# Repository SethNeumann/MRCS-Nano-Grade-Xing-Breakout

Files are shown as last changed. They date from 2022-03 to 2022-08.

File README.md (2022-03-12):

# REPO NAME: MRCS-Nano-Grade-Xing-Breakout

## License: Creative Commons Attribution-NonCommercial-ShareAlike

There are plenty of good Arduino Grade Xing sketches. This board supports one by Jon Schmidt which uses the Nano's 8
analog inputs to monitor up 4 sets of sensors. It drives 2 servos for the crossing gates, 2 phases of LEDs
for the flashing lights and an output to drive a crossing bell sound module, like the ones from our friends
at Iowa Scaled Engineering.

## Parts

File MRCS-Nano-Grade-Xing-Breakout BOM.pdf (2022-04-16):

Qty | Value | Device | Package | Parts | Description
2 | CONNECTOR-M08LOCK | 1X08_LOCK | SENSOR0-3, SENSOR4-7 | Header 8
2 | M03LOCKx2 | 22X03_LOCK | A6, A7, SERVO1, SERVO2 | Header 3
2 | RPTH-R0 | CUT-R | R8, R9 | cuttable Resistor pad
| 1 .1 @ 25V | CAPPTH2 | C-PTH-0.100 | C2
| 2 10K | TRIM_US-RS3 | RS3 | R1, R2 | POTENTIOMETER
1 470 uF @ 16V CAP-POLPTH-3.5MM | E3.5-10 | C1
| 1 4700 | G08R | SIL9 | RN1 | SIL RESISTOR
| 1 5V PWR | CONNECTOR-DC-POWER-RA | DCJ0202 | J1 | DC POWER JACK
| 1 5V PWR | CONNECTOR-M04SCREW_LOCK | SCREWTERMINAL-3.5MM-4_LOCK | CON1 | Header 4
| 1 NANO | NANO | NANO | U$1 | Arduino Nano
| 1 Outputs | CONNECTOR-M08LOCK | 1X08_LOCK | J4 | Header 8
| 0 Unused I/O | CONNECTOR-M08LOCK | 1X08_LOCK | J2 | Header 8
| 2 15 pin | 0.100 x 15 female header | | N1, N2 | Nano Header
| 1 PCB | Grade Xing Controller | 69x99 | | PCB

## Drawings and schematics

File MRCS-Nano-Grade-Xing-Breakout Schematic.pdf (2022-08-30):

A

A

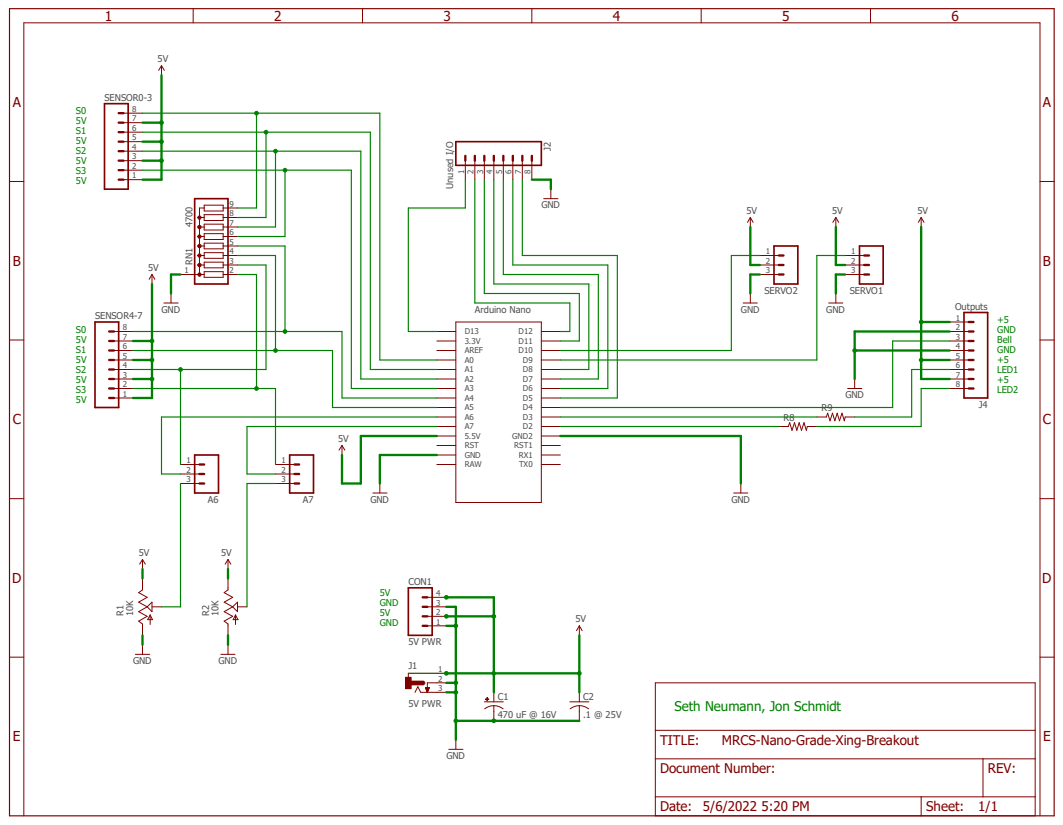
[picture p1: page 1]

Seth Neumann, Jon Schmidt

MRCS-Nano-Grade-Xing-Breakout

Document Number: | REV:

Date: 5/6/2022 5:20 PM | Sheet: 1/1

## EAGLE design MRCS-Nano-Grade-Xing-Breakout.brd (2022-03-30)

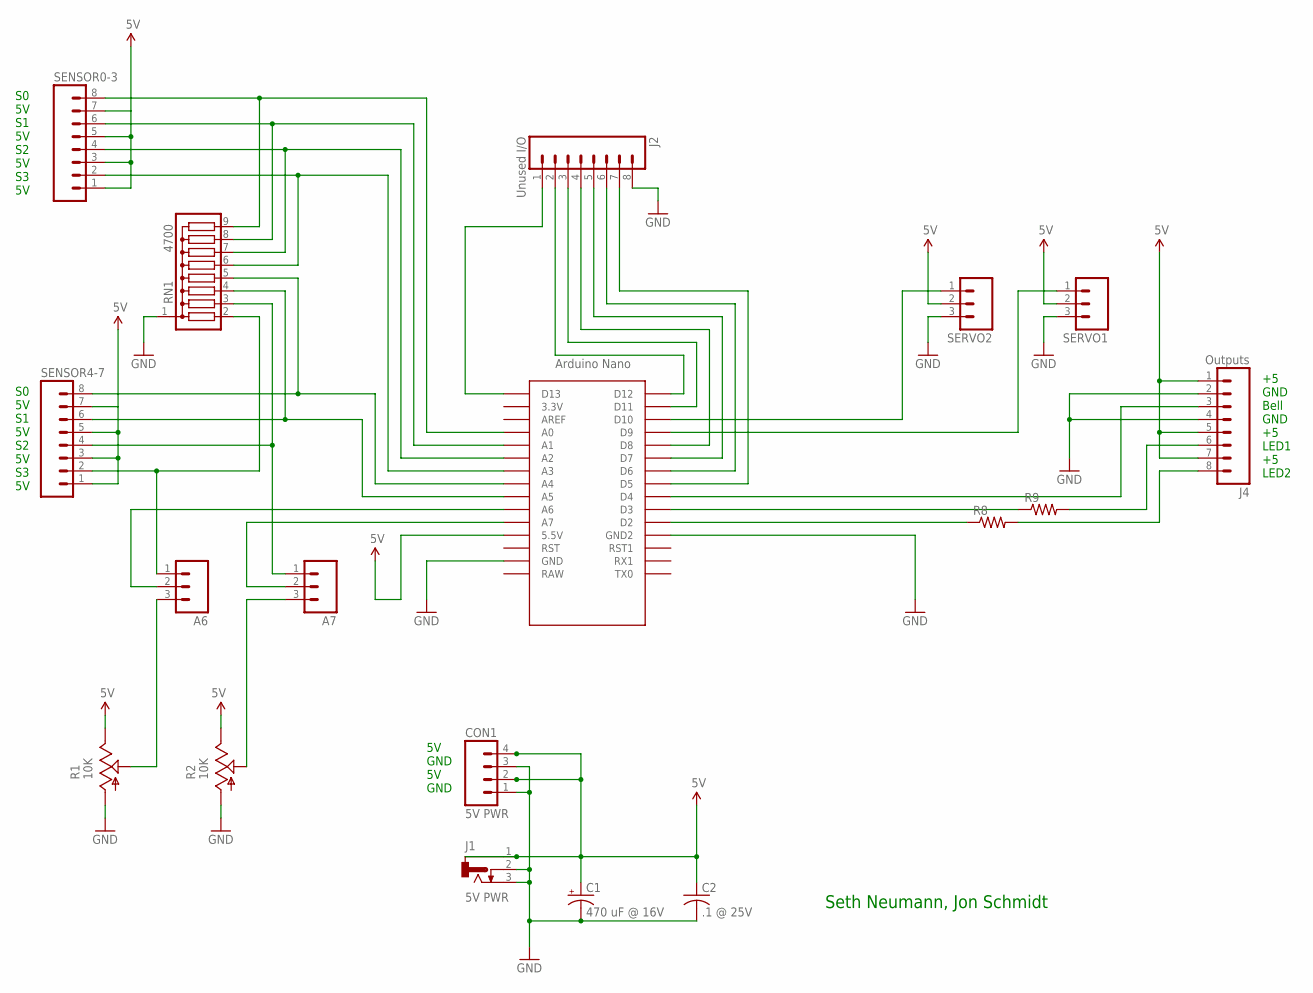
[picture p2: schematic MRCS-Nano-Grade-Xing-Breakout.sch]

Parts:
A6, A7: M03LOCK; 1X03_LOCK
C1: 470 uF @ 16V; E3.5-10
C2: .1 @ 25V; C-PTH-0.100
CON1: 5V PWR; SCREWTERMINAL-3.5MM-4_LOCK
J1: 5V PWR; DCJ0202
J2: Unused I/O; 1X08_LOCK
J4: Outputs; 1X08_LOCK
R1, R2: 10K; RS3
R8, R9: RPTH-R0; CUT-R
RN1: 4700; SIL9
SENSOR0-3, SENSOR4-7: CONNECTOR-M08LOCK; 1X08_LOCK
SERVO1, SERVO2: M03LOCK; 1X03_LOCK
U$1: NANO

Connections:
5V: C1.+, C2.1, CON1.2, CON1.4, J1.1, J4.1, J4.5, J4.7, R1.E, R2.E, SENSOR0-3.1, SENSOR0-3.3, SENSOR0-3.5, SENSOR0-3.7, SENSOR4-7.1, SENSOR4-7.3, SENSOR4-7.5, SENSOR4-7.7, SERVO1.2, SERVO2.2, U$1.5V (5.5V)
A0: RN1.9, SENSOR0-3.8, U$1.A0
GND: C1.-, C2.2, CON1.1, CON1.3, J1.2, J1.3, J2.8, J4.2, J4.4, R1.A, R2.A, RN1.1, SERVO1.3, SERVO2.3, U$1.GND, U$1.GND1 (GND2)
unnamed: RN1.5, SENSOR4-7.8, U$1.A4
unnamed: R8.P2 (1), U$1.D2
unnamed: J4.8, R8.P1 (2)
unnamed: R9.P2 (1), U$1.D3
unnamed: J4.6, R9.P1 (2)
unnamed: J4.3, U$1.D4
unnamed: RN1.4, SENSOR4-7.6, U$1.A5
unnamed: SERVO2.1, U$1.D10
unnamed: SERVO1.1, U$1.D9
unnamed: RN1.7, SENSOR0-3.4, U$1.A2
unnamed: A7.1, RN1.3, SENSOR4-7.4
unnamed: RN1.6, SENSOR0-3.2, U$1.A3
unnamed: A6.1, RN1.2, SENSOR4-7.2
unnamed: A6.3, R1.S
unnamed: A6.2, U$1.A6
unnamed: A7.2, U$1.A7
unnamed: RN1.8, SENSOR0-3.6, U$1.A1
unnamed: A7.3, R2.S
unnamed: J2.1, U$1.D13
unnamed: J2.2, U$1.D12
unnamed: J2.3, U$1.D11
unnamed: J2.4, U$1.D8
unnamed: J2.5, U$1.D7
unnamed: J2.6, U$1.D6
unnamed: J2.7, U$1.D5

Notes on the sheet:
5V GND 5V GND
Seth Neumann, Jon Schmidt
S0 5V S1 5V S2 5V S3 5V
+5 GND Bell GND +5 LED1 +5 LED2

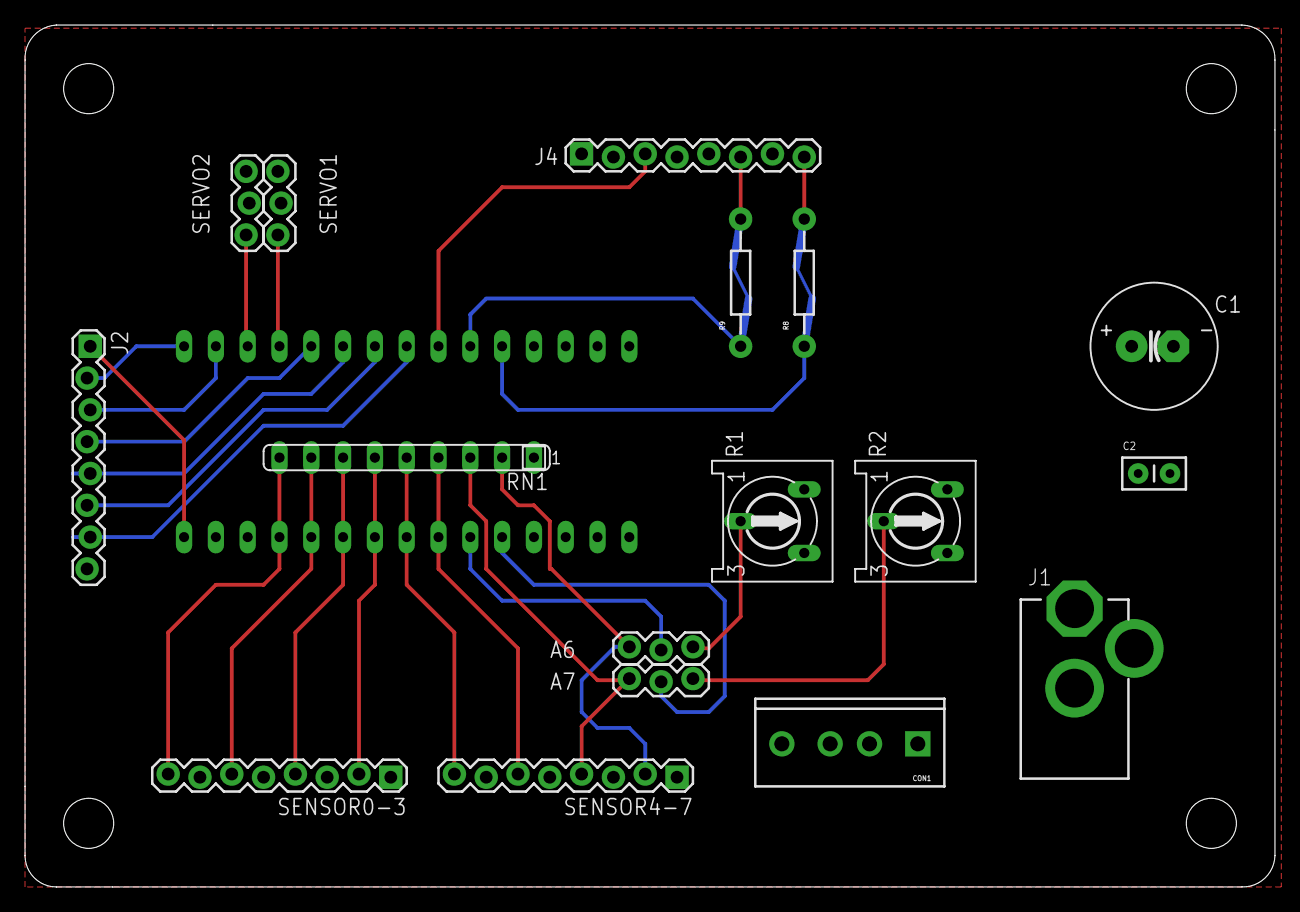
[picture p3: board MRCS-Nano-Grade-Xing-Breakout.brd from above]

Board: 2 copper layers, 99.8 x 68.8 mm, 21 parts (0 on the bottom side), 28 nets.

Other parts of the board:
U$2: CA-PROP65WARNING
U$3: MRCSLOGOTOP
U$10: BOARD-DINRAIL-2.7IN

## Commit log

2022-03-12 initial commit
    started from the PCR Clinic board
    [EagleTemplate-new.brd, EagleTemplate-new.sch, MRCS-Nano-Grade-Xing-Breakout.brd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]
2022-03-15 completed initial deisgn
    After some consultation with Jon Schmidt this is ready to try for fab
    [MRCS-Nano-Grade-Xing-Breakout.brd, MRCS-Nano-Grade-Xing-Breakout.sch]
2022-03-16 fixed a few labels per Jon S
    [MRCS-Nano-Grade-Xing-Breakout.brd]
2022-03-30 gerb files for first build
    [MRCS-Nano-Grade-Xing-Breakout.brd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]
2022-03-30 relects first board
2022-04-16 clean up for listing product on site
    removed individual gerb files, use the zip
    added pdf of BOM
    [MRCS-Nano-Grade-Xing-Breakout.GBL, MRCS-Nano-Grade-Xing-Breakout.GBO, MRCS-Nano-Grade-Xing-Breakout.GBS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]
2022-05-07 cleanup of minor issues mostly A6 A7 jumpers
    these allow you to use either on board pots to set limits for servo movement for the crossing gates or to use A6,A7 for additional sensors with pull downs. A6 and A7 were reversed, so the traces were adjusted
    [MRCS-Nano-Grade-Xing-Breakout.GBL, MRCS-Nano-Grade-Xing-Breakout.GBO, MRCS-Nano-Grade-Xing-Breakout.GBS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]
2022-08-30 Create MRCS-Nano-Grade-Xing-Breakout Schematic.pdf

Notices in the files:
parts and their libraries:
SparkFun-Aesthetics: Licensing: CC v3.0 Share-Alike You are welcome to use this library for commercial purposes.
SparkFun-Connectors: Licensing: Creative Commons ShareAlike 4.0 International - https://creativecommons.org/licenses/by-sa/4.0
